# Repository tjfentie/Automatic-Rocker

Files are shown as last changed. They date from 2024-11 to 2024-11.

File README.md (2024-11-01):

# Automatic-Rocker
Mechanism that attaches to a rocking chair and automatically rocks with speed control and overcurrent protection

Video that explains everything found here: https://youtu.be/azg7B9vxmTY

Published under a Creative Commons Attribution-ShareAlike 4.0 license https://creativecommons.org/licenses/by-sa/4.0/ (CC BY-SA 4.0).

The documentation template was created by Makers Making Change / Neil Squire Society and is used under a CC BY-SA 4.0 license. It is available at the following link: https://github.com/makersmakingchange/OpenAT-Template

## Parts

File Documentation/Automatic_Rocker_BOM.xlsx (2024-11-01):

Device: | Automatic Rocker
Version: | V 4.0
Last Updated: | 2024-11-01
 |  |  |  |  |  |  |  | Total filament (g) |  | Unit Cost | Total Estimated Cost | Build Cost
 |  |  |  |  |  |  |  | 1501 |  | $457.14 | $611.47
ID | Commercial Parts |  |  |  |  |  |  |  |  | $413.82 | $544.94
 | Part | Description |  | Manufacturer | Supplier | QTY / Device | QTY / PKG | PKGs | $/ PKG | $ / Device | Total Estimated Cost |  | Link
 | 12V motor | Right angle reversable 45 RPM |  |  | amazon | 1 | 1 | 1 | $128.39 | $128.39 | $128.39 |  | https://www.amazon.ca/dp/B01E86DORM?ref=ppx_yo2ov_dt_b_fed_asin_title
 | 12V power supply |  |  |  | amazon | 1 | 1 | 1 | $16.73 | $16.73 | $16.73 |  | https://www.amazon.ca/dp/B0711Q5B49?ref=ppx_yo2ov_dt_b_fed_asin_title
 | 5V relay |  |  |  | amazon | 1 | 5 | 1 | $14.36 | $2.87 | $14.36 |  | https://www.amazon.ca/dp/B07DN8WTKX?ref=ppx_yo2ov_dt_b_fed_asin_title
 | 30A current sensor |  |  |  | amazon | 1 | 2 | 1 | $15.99 | $8.00 | $15.99 |  | https://www.amazon.ca/dp/B07SPRL8DL?ref=ppx_yo2ov_dt_b_fed_asin_title
 | Dupont wires |  |  |  | amazon | 30 | 120 | 1 | $13.64 | $3.41 | $13.64 |  | https://www.amazon.ca/dp/B01EV70C78?ref=ppx_yo2ov_dt_b_fed_asin_title
 | DC power connector | 5.5x2.1 |  |  | amazon | 1 | 2 | 2 | $8.95 | $4.47 | $17.90 |  | https://www.amazon.ca/dp/B07JMY5XXT?ref=ppx_yo2ov_dt_b_fed_asin_title
 | Motor Driver | L298 |  |  | amazon | 1 | 1 | 1 | $26.99 | $26.99 | $26.99 |  | https://www.amazon.ca/dp/B06XGD5SCB?ref=ppx_yo2ov_dt_b_fed_asin_title
 | Tactile Push buttons |  |  |  | amazon | 1 | 25 | 1 | $13.88 | $0.56 | $13.88 |  | https://www.amazon.ca/dp/B01E38OS7K?ref=ppx_yo2ov_dt_b_fed_asin_title
 | Rocker Switch |  |  |  | amazon | 1 | 5 | 1 | $7.99 | $1.60 | $7.99 |  | https://www.amazon.ca/dp/B07Y1GDRQG?ref=ppx_yo2ov_dt_b_fed_asin_title
 | 10K Ohm Potentiometer |  |  |  | amazon | 1 | 60 | 1 | $15.74 | $0.26 | $15.74 |  | https://www.amazon.ca/dp/B07B64MWRF?ref=ppx_yo2ov_dt_b_fed_asin_title
 | M6 Connector Nut | Try to find one M6x10x10 |  |  | amazon | 1 | 5 | 1 | $12.59 | $2.52 | $12.59 |  | https://www.amazon.ca/dp/B09MWHYG1M?ref=ppx_yo2ov_dt_b_fed_asin_title&th=1
 | Fan | 40x40 |  |  | amazon | 1 | 5 | 1 | $12.64 | $2.53 | $12.64 |  | https://www.amazon.ca/dp/B0757LXKST?ref=ppx_yo2ov_dt_b_fed_asin_title
 | RAM claw | 1inch ram components |  |  | amazon | 1 | 1 | 1 | $43.99 | $43.99 | $43.99 |  | https://www.amazon.ca/dp/B00JQNRTDI?ref=ppx_yo2ov_dt_b_fed_asin_title
 | RAM U bolt |  |  |  | amazon | 1 | 1 | 1 | $29.99 | $29.99 | $29.99 |  | https://www.amazon.ca/dp/B0BXC7FGJL?ref=ppx_yo2ov_dt_b_fed_asin_title
 | RAM double socket | small |  |  | amazon | 1 | 1 | 1 | $13.59 | $13.59 | $13.59 |  | https://www.amazon.ca/dp/B0BN9LPZY3?ref=ppx_yo2ov_dt_b_fed_asin_title&th=1
 | Shoulder bolt | M6x40 |  |  | amazon | 1 | 5 | 1 | $18.49 | $3.70 | $18.49 |  | https://www.amazon.ca/dp/B077GXPR5R?ref=ppx_yo2ov_dt_b_fed_asin_title
 | Crank arm |  |  |  | amazon | 1 | 1 | 1 | $25.99 | $25.99 | $25.99 |  | https://www.amazon.ca/dp/B0BS6T9L2P?ref=ppx_yo2ov_dt_b_fed_asin_title&th=1
 | Aluminum spacers |  |  |  | amazon | 7 | 10 | 1 | $12.00 | $8.40 | $12.00 |  | https://www.amazon.ca/dp/B0CX1R97GR?ref=ppx_yo2ov_dt_b_fed_asin_title
 | Protoboard | any board will do. The cad is for this one though. |  |  | local shop | 1 | 1 | 1 | $15.59 | $15.59 | $15.59 |  | https://www.solarbotics.com/product/20908
 | 1/4 inch Plywood |  |  |  | home depot | 1 | 1 | 1 | $17.51 | $17.51 | $17.51 |  | https://www.homedepot.ca/product/alexandria-moulding-1-4-inch-x-2-feet-x-4-feet-birch-plywood-handy-panel/1000114111
 | Bearings | standard skateboard size |  |  | Bones | 2 | 8 | 1 | $18.95 | $4.74 | $18.95 |  | https://bonesbearings.com/bonesr-redsr-skateboard-bearings-8-pack
 | arduino Uno rev 3 |  |  |  | arduino | 1 | 1 | 1 | $52.00 | $52.00 | $52.00 |  | https://store.arduino.cc/products/arduino-uno-rev3
 | 3D Printed Parts |  |  |  |  |  |  | 1503 |  | $37.52 | $37.52
 | Part | Description | Filament Type | Filament | Color | QTY / Device | Mass (g) / Part | Total Mass | $ / kg | $ / Device | Total Estimated Cost |  | Link
 | All components | There are 13 total parts to print | PLA |  | Any | 1 | 1501 | 1501 | $25.00 | $37.52 | $37.52
 |  |  |  |  |  |  |  | 0 |  | $0.00 | $0.00
 |  |  |  |  |  |  |  | 0 |  | $0.00 | $0.00
 |  |  |  |  |  |  |  | 0 |  | $0.00 | $0.00
 |  |  |  |  |  |  |  | 0 |  | $0.00 | $0.00
 |  |  |  |  |  |  |  | 0 |  | $0.00 | $0.00
 |  |  |  |  |  |  |  | 0 |  | $0.00 | $0.00
 |  |  |  |  |  |  |  | 0 |  | $0.00 | $0.00
 | Custom PCB |  |  |  |  |  |  |  |  | $5.80 | $29.00
 | Part | Description |  | Manufacturer | Supplier | QTY / Device | QTY / PKG | PKGs | $/ PKG | $ / Device | Total Estimated Cost |  | Link
 |  |  |  |  |  | 1 | 5 | 1 | $4.00 | $0.80 | $4.00
 |  | Shipping |  |  |  | 1 | 5 | 1 | $25.00 | $5.00 | $25.00
 | Tools
 | Tool | Description |  | Manufacturer | Supplier |  |  |  |  |  |  |  | Link
 | Soldering iron
 | some type of saw
 | sandpaper
 | 3D printer
 | common hand tools
 | Alternatives
 | Part | Description |  | Manufacturer | Supplier | QTY / Device | QTY / PKG | PKGs | $/ PKG | $ / Device | Total Estimated Cost |  | Link

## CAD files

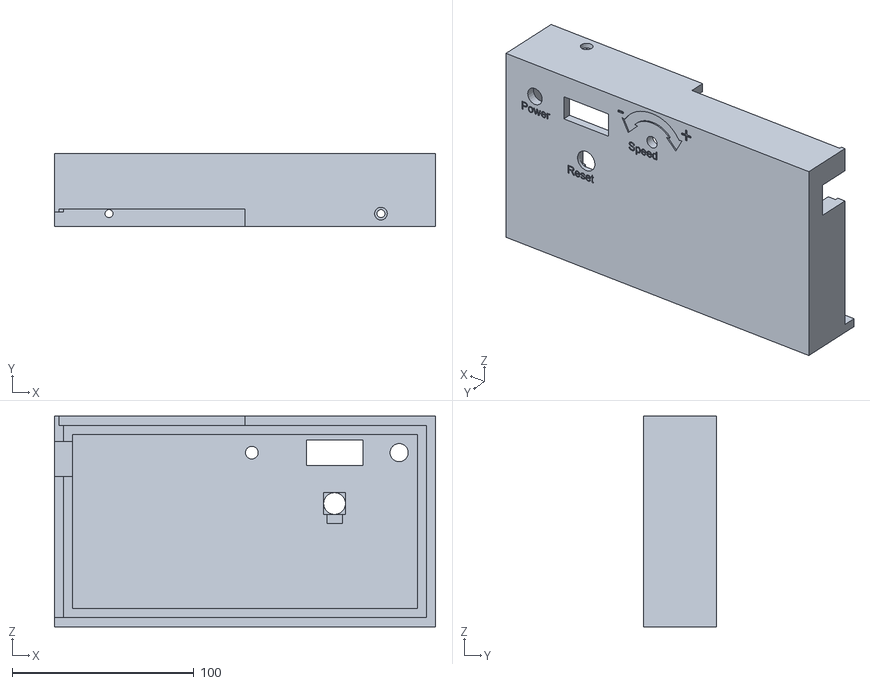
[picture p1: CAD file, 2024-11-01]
3D-Print-Files/Electronic-Enclosure-Lid.stl
209.5 x 40.0 x 115.8

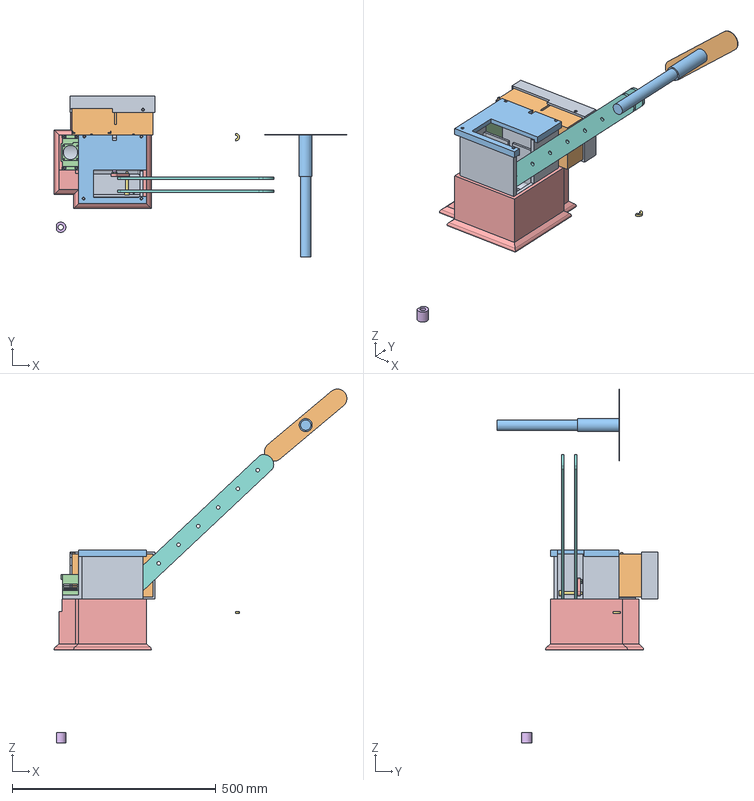
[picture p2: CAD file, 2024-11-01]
Build-Files/Automatic_Rocker_v4.step
718.1 x 394.0 x 868.1 mm
Enclosure Base
Rocker Path
pseudo-bar
M6x10 Coupler nut
Crank
Motor connection
M6x40shoulder bolt
Linkage 2 x 2
Electronic enclosure lid
Main Enclosure Lid
Sliding Motor Lid
weighted base
spacer covers
spacer fior shoulder bolt

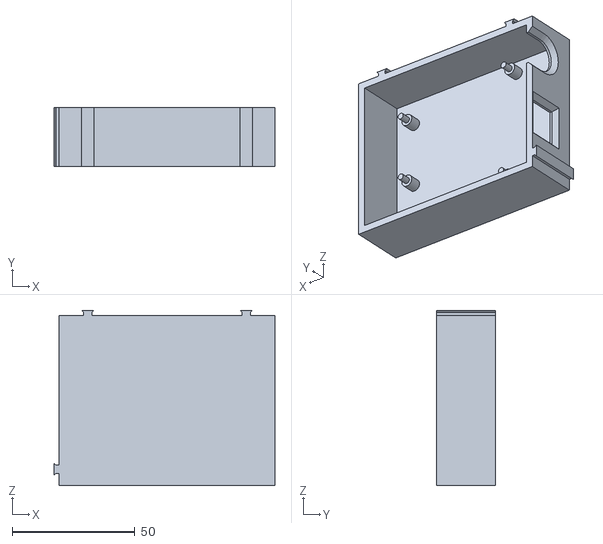
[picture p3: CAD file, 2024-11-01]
3D-Print-Files/Arduino-Housing.stl
89.9 x 24.0 x 71.3

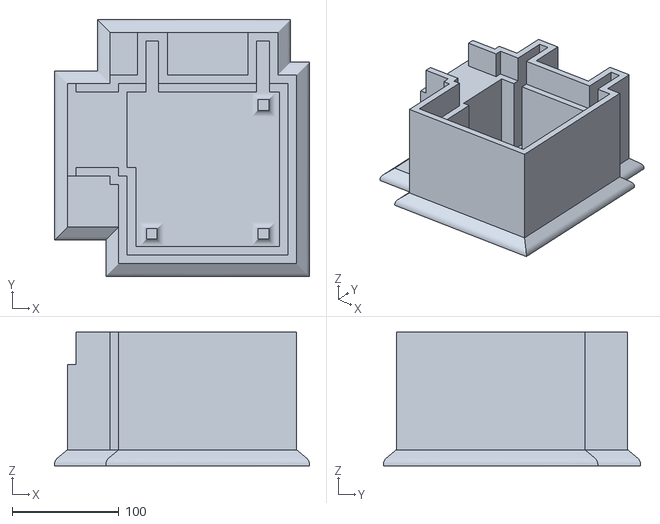
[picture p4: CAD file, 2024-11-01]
3D-Print-Files/Weighted-Base.stl
238.5 x 240.5 x 125.0

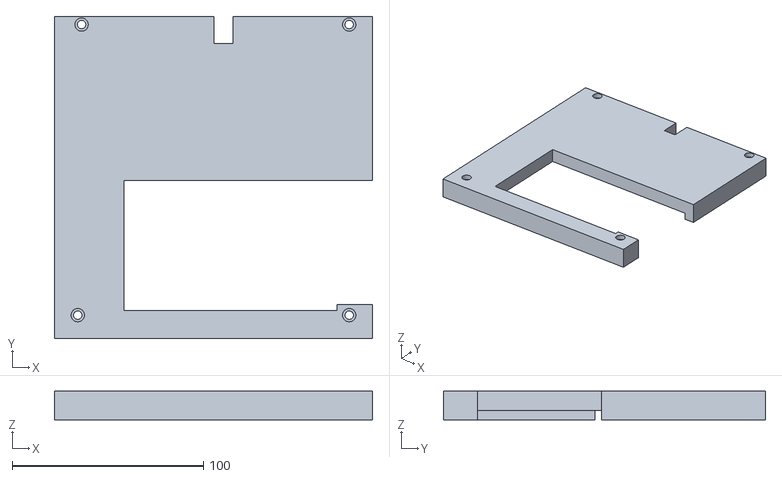
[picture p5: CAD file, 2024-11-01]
3D-Print-Files/Motor-Enclosure-Lid.stl
166.5 x 168.4 x 15.0

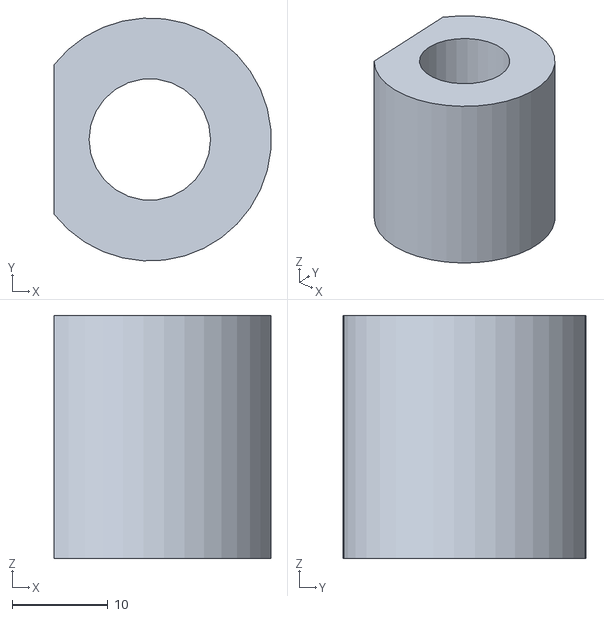
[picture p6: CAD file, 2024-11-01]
3D-Print-Files/Spacer Covers.stl
22.7 x 25.4 x 25.4

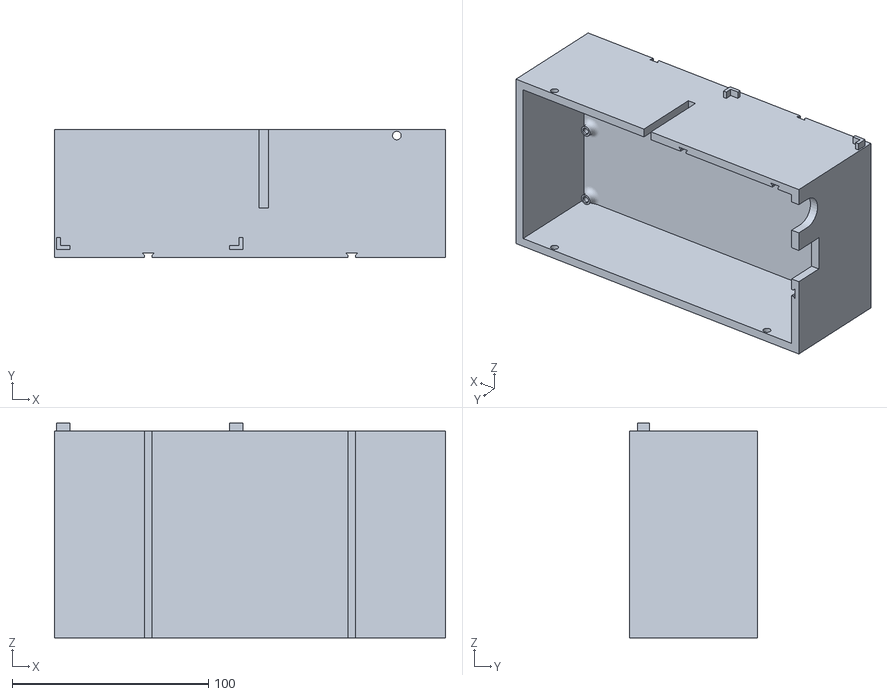
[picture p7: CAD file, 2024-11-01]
3D-Print-Files/Electronic-Enclosure-Base.stl
199.0 x 65.0 x 109.3

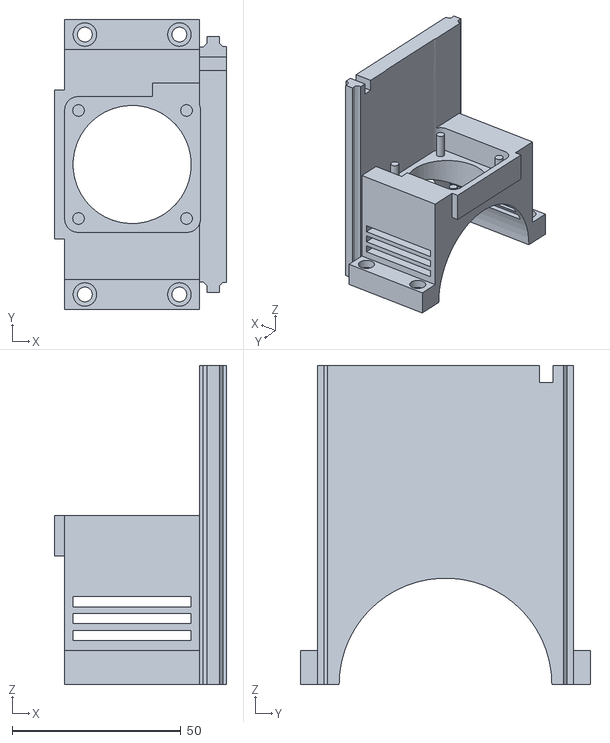
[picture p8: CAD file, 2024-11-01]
3D-Print-Files/Sliding-Motor-Cover.stl
51.0 x 86.0 x 94.5

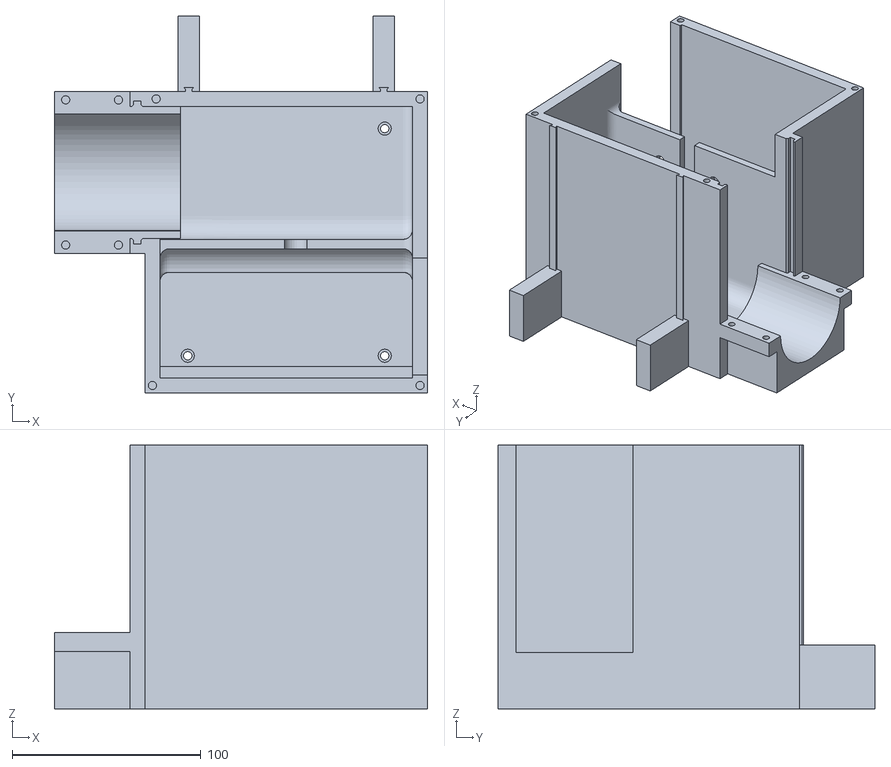
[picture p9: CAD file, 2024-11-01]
3D-Print-Files/Motor-Housing.stl
198.0 x 200.0 x 140.0

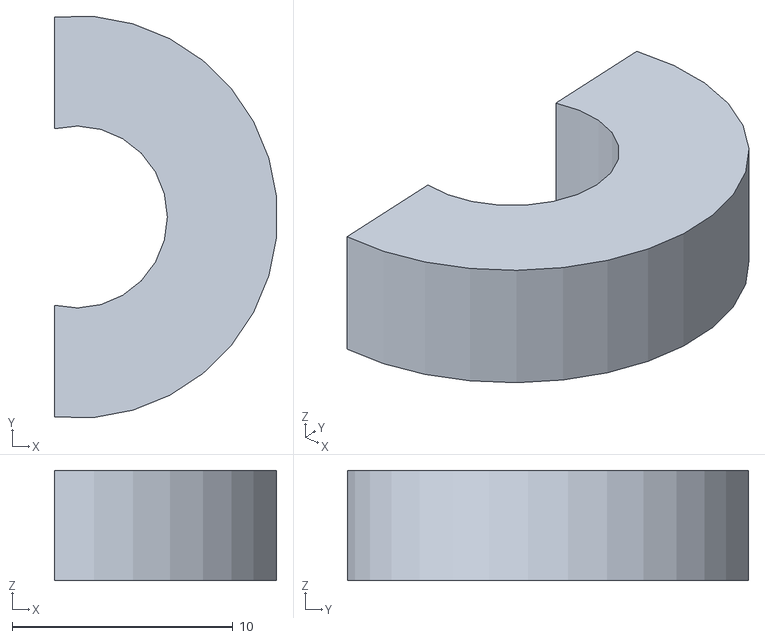
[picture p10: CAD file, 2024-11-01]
3D-Print-Files/Shoulder-Bolt-Spacer.stl
10.1 x 18.2 x 5.00

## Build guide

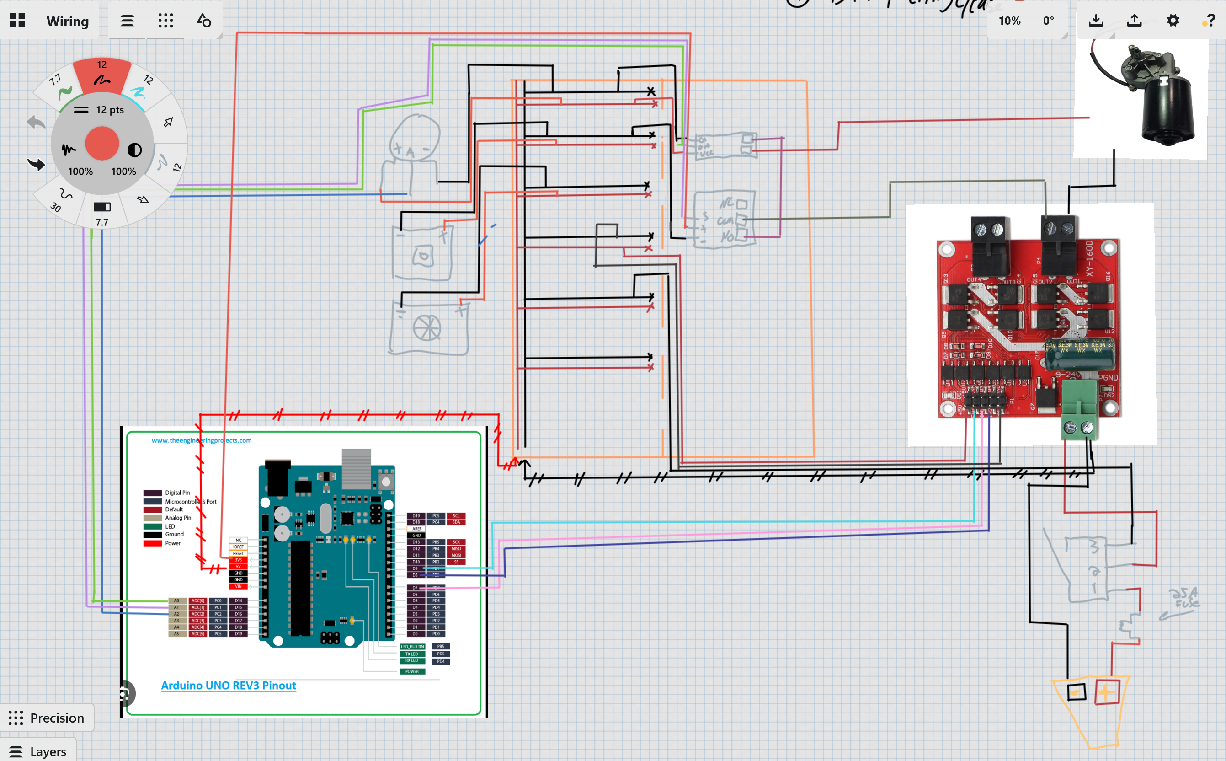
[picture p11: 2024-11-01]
Electronics/wiring.png

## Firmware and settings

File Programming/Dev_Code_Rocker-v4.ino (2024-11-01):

// Aug 25, 2024
// Pin Definitions
int IN1pin = 7;  // Motor driver IN1 pin
int IN2pin = 8;  // Motor driver IN2 pin
int ENApin = 9;  // Motor driver ENA pin (PWM)
int RelayPin = A1;  // Relay control pin
int analogPin = A0;  // Current sensor output pin
int potPin = A2;  // Potentiometer input pin
int buttonPin = 3;  // Tactile button input pin

// Variables
long int sensorValue = 0;  // Variable to store the current sensor value
int potValue = 0;  // Variable to store the potentiometer value
int motorSpeed = 0;  // Variable to store the motor speed (PWM value)
bool motorStopped = false;  // Flag to indicate if the motor is stopped

void setup() {
  // Configure Arduino pins as outputs
  pinMode(IN1pin, OUTPUT);
  pinMode(IN2pin, OUTPUT);
  pinMode(ENApin, OUTPUT);
  pinMode(RelayPin, OUTPUT);
  pinMode(buttonPin, INPUT_PULLUP);  // Set button pin as input with internal pull-up resistor

  // Set Timer1 to Fast PWM mode for the motor driver
  TCCR1B = TCCR1B & 0b11111000 | 0x01;

  // Ensure the relay is initially allowing power (NC state)
  digitalWrite(RelayPin, HIGH);

  // Initialize serial communication for debugging
  Serial.begin(9600);
  delay(100); // Small delay to stabilize serial communication
}

void loop() {
  // Read the potentiometer value
  potValue = analogRead(potPin);

  // Map the potentiometer value (0-1023) to the desired PWM range (100-255)
  motorSpeed = map(potValue, 0, 1023, 100, 255);

  // Read the current sensor value
  sensorValue = analogRead(analogPin);

  // Output the sensor value to the Serial Monitor
  Serial.print("ADC Value: ");
  Serial.println(sensorValue);

  // Output the motor speed to the Serial Monitor
  Serial.print("Motor Speed: ");
  Serial.println(motorSpeed);

  // Check if the motor is currently stopped
  if (motorStopped) {
    // Check if the button is pressed (LOW state)
    if (digitalRead(buttonPin) == LOW) {
      motorStopped = false;  // Reset the flag to allow motor operation
      delay(200);  // Debounce delay
    }
  } else {
    // Overload protection: check if the sensor value exceeds the threshold
    if (sensorValue > 600) {  // Adjust threshold based on your observed readings
      digitalWrite(RelayPin, LOW);  // Activate relay to open the circuit and stop the motor
      motorStopped = true;  // Set the flag to indicate the motor is stopped
    } else {
      digitalWrite(RelayPin, HIGH);  // Deactivate relay to close the circuit and allow motor operation

      // Turn the motor in one direction with the PWM value set by the potentiometer
      digitalWrite(IN1pin, HIGH);
      digitalWrite(IN2pin, LOW);
      analogWrite(ENApin, motorSpeed);  // Set motor speed based on potentiometer input
    }
  }

  // Set a delay to allow time for readings
  delay(200);
}
